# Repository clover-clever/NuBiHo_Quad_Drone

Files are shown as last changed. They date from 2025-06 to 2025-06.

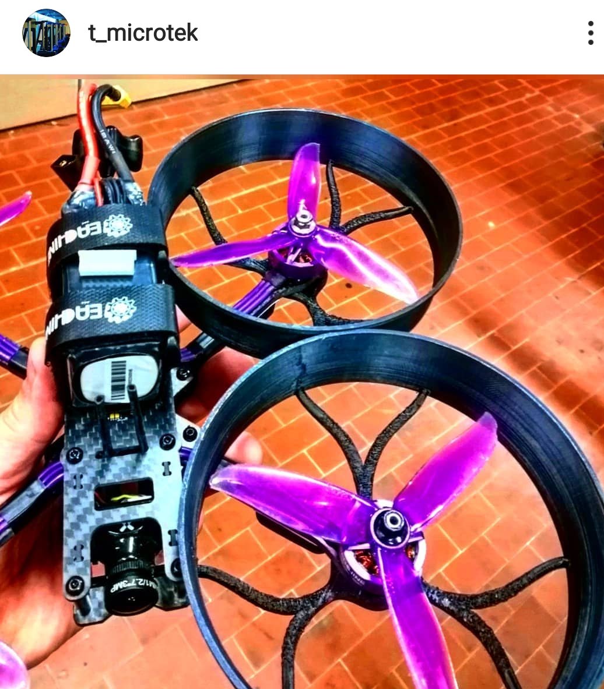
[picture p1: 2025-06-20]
NuBiHo_HW/Universal Propeller Guard Cover 5 inch - 4013765/images/Polish_20191201_160728039.jpg

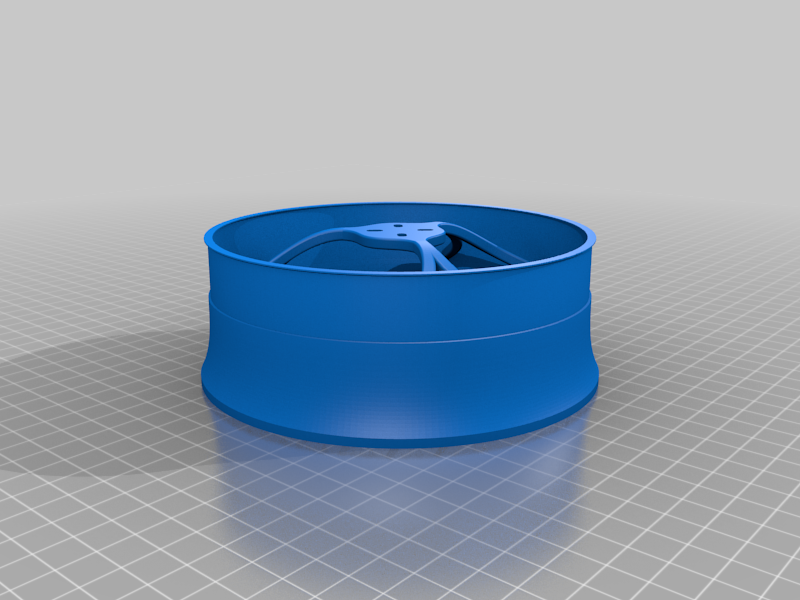
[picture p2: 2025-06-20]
NuBiHo_HW/Universal Propeller Guard Cover 5 inch - 4013765/images/propellers_cover_5inch_support.png

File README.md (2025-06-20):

2025, first semester Microprocessor Quad Drone Project

Based on Arduino Uno R3 for control with PPM Signal

PPM for SPRacing R3

Self-made PCBs
  - 6V Regulator does not work well,(Burnt)(delete 6V Switching Regulator and use it)
  - LM1117 - 12V --> 5V(too big voltage difference, do not use for high load, or just do not use it)

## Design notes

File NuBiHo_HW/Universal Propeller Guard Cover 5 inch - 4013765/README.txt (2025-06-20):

Universal Propeller Guard Cover 5 inch by TMicrotek on Thingiverse: https://www.thingiverse.com/thing:4013765

Summary:
Universal propeller guard will protect your propellers from impacts.One program already has the supports,while in the other you will have to insert them in the slicing program.If you like my things and want to support me, tips are welcome :)Have fun!

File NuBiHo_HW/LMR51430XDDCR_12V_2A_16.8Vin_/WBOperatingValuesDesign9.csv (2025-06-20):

Name | Value | Category | Description
Vout | 12 V | System Information | Operational Output Voltage
IC Tolerance | 10 mV | IC | IC Feedback Tolerance
Cin IRMS | 790.21 mA | Capacitor | Input capacitor RMS ripple current
Cin Pd | 4.16 mW | Capacitor | Input capacitor power dissipation
Cout IRMS | 30.67 mA | Capacitor | Output capacitor RMS ripple current
Cout Pd | 423.37 µW | Capacitor | Output capacitor power dissipation
Coutx IRMS | 56 mA | Capacitor | Output capacitor_x RMS ripple current
Coutx Pd | 13.23 µW | Capacitor | Output capacitor_x power loss
Cinx IRMS | 101.96 mA | Capacitor | Bulk capacitor RMS ripple current
Cinx Pd | 10.39 µW | Capacitor | Bulk capacitor power dissipation
L Ipp | 300.24 mA | Inductor | Peak-to-peak inductor ripple current
L Pd | 84.16 mW | Inductor | Inductor power dissipation
Ipp percentage | 15.01% | Inductor | Inductor ripple current percentage (with respect to average inductor current)
Duty Cycle | 72.89% | System Information | Duty cycle
Efficiency | 97% | System Information | Steady state efficiency
Frequency | 500 kHz | System Information | Switching frequency
IC Tj | 77.11 °C | IC | IC junction temperature
IC Pd | 654.32 mW | IC | IC power dissipation
Pout | 24 W | System Information | Total output power
Iin Avg | 1.47 A | IC | Average input current
IC Ipk | 2.15 A | IC | Peak switch current in IC
Mode | CCM | System Information | Conduction Mode
Vout p-p | 47.81 mV | System Information | Peak-to-peak output ripple voltage
Vin p-p | 961.15 mV | System Information | Peak-to-peak input voltage
Phase Marg | 48.62 ° | System Information | Bode Plot Phase Margin
Cross Freq | 15.55 kHz | System Information | Bode plot crossover frequency
Low Freq Gain | 46.85 dB | System Information | Gain at 1Hz
Gain Marg | -24.07 dB | System Information | Bode Plot Gain Margin
ICThetaJA Effective | 72 °C/W | IC | Effective IC Junction-to-Ambient Thermal Resistance
Total Pd | 743.28 mW | Power | Total Power Dissipation
FootPrint | 460 mm² | System Information | Total Foot Print Area of BOM components
Vin | 16.8 V | System Information | Vin operating point
Iout | 2 A | System Information | Iout operating point
Cin Pd | 4.16 mW | Power | Input capacitor power dissipation
Cout Pd | 423.37 µW | Power | Output capacitor power dissipation
Coutx Pd | 13.23 µW | Power | Output capacitor_x power loss
Cinx Pd | 10.39 µW | Power | Bulk capacitor power dissipation
L Pd | 84.16 mW | Power | Inductor power dissipation
IC Pd | 654.32 mW | Power | IC power dissipation
Vout Actual | 12.06 V | System Information | Vout Actual calculated based on selected voltage divider resistors
Vout Tolerance | 3.62% | System Information | Vout Tolerance based on IC Tolerance (no load) and voltage divider resistors if applicable
Total BOM | $3.36 | System Information | Total BOM Cost
BOM Count | 11 | System Information | Total Design BOM count

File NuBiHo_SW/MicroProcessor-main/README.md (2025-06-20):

# MicroProcessor

## Team
- 김민우
- 김재영
- 이상훈

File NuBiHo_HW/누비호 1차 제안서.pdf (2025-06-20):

# 마이크로프로세서응용시스템 제안서 발표

4조

### 2020099052 김재영 2020063063 김민우 2020028659 이상훈

# 누비호

## 1.문제 인식 배경

## 2.구현 목표

## 3.예상되는 어려움

## 4.구매 예정 물품

## 5.추후 계획

# CONTENTS

# 01 문제 인식 배경

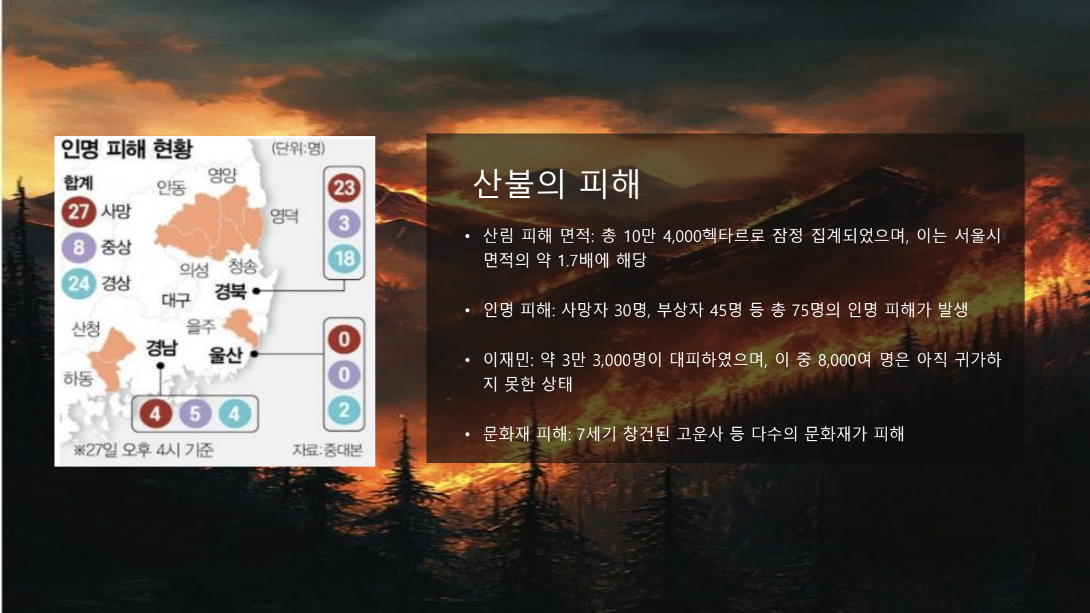
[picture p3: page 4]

Hong Hyun You 4

# 산불의 피해

- 산림 피해 면적: 총 10만 4,000헥타르로 잠정 집계되었으며, 이는 서울시 면적의 약 1.7배에 해당
- 인명 피해: 사망자 30명, 부상자 45명 등 총 75명의 인명 피해가 발생
- 이재민: 약 3만 3,000명이 대피하였으며, 이 중 8,000여 명은 아직 귀가하 지 못한 상태
- 문화재 피해: 7세기 창건된 고운사 등 다수의 문화재가 피해

## 문제 인식 배경

## 산악지형 접근성

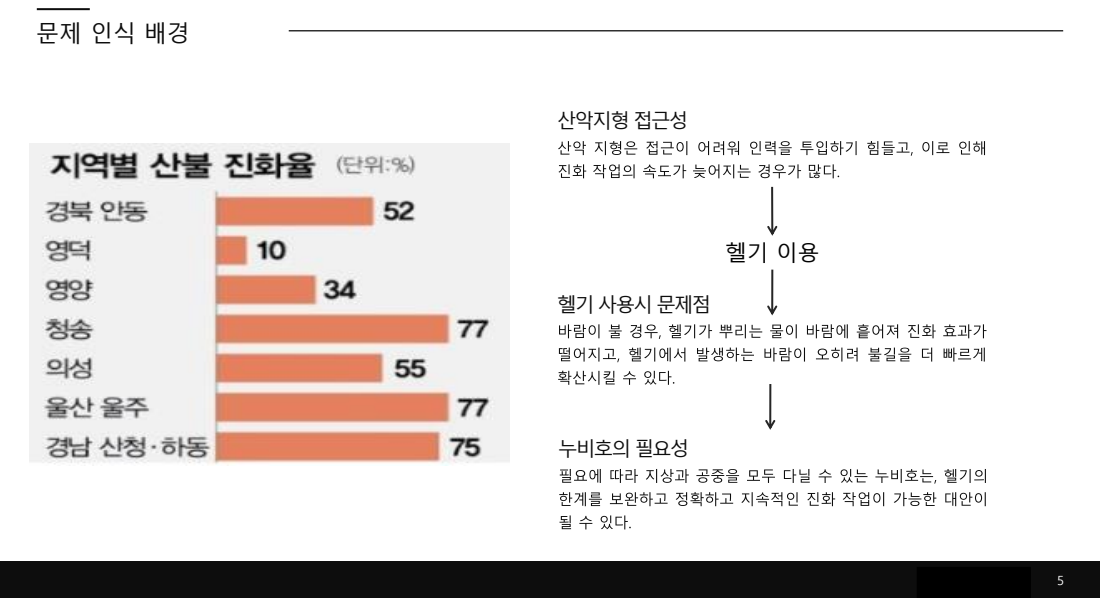
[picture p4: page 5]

산악 지형은 접근이 어려워 인력을 투입하기 힘들고, 이로 인해
진화 작업의 속도가 늦어지는 경우가 많다.

헬기 사용시 문제점
바람이 불 경우, 헬기가 뿌리는 물이 바람에 흩어져 진화 효과가
떨어지고, 헬기에서 발생하는 바람이 오히려 불길을 더 빠르게
확산시킬 수 있다.

누비호의 필요성
필요에 따라 지상과 공중을 모두 다닐 수 있는 누비호는, 헬기의
한계를 보완하고 정확하고 지속적인 진화 작업이 가능한 대안이

# 02 구현 목표

## 구현 목표

## 육공 양용 기능

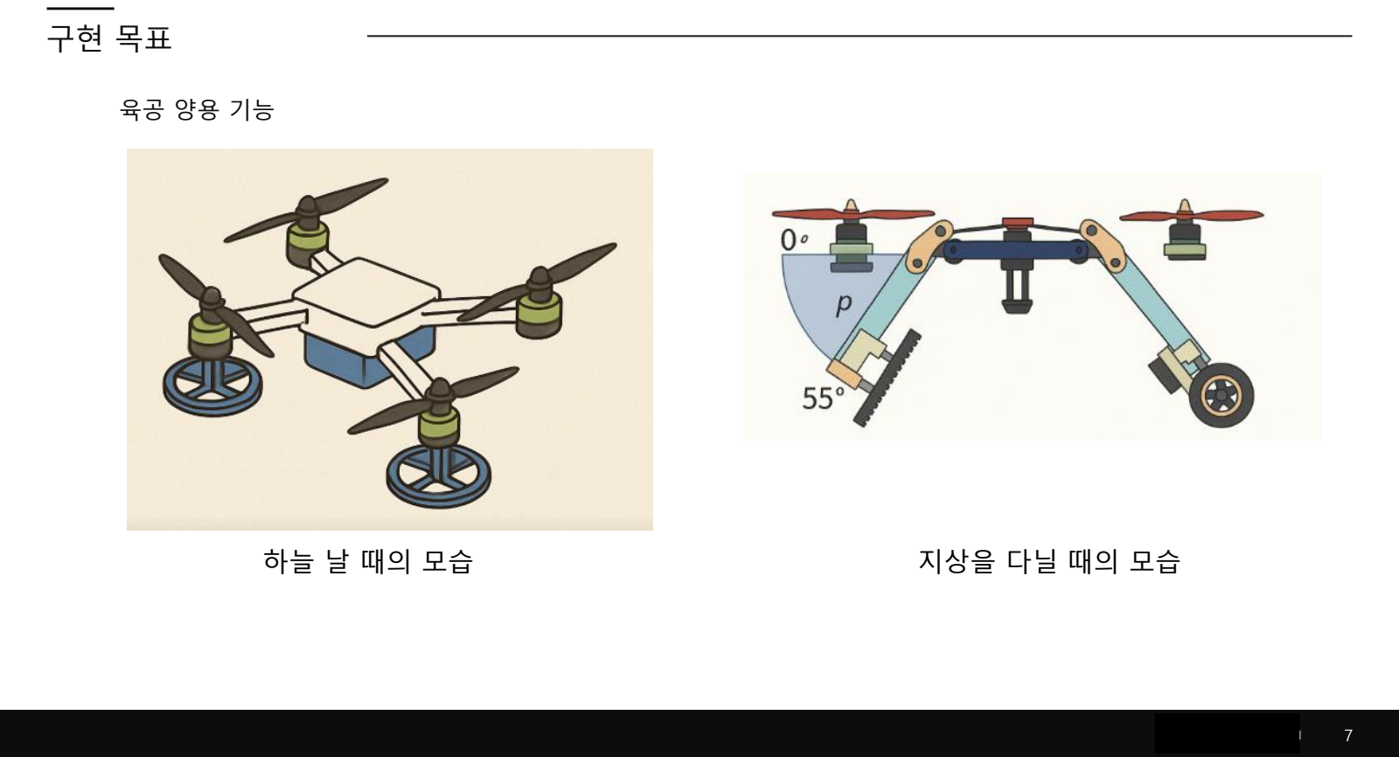
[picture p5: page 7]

하늘 날 때의 모습 | 지상을 다닐 때의 모습

## 구현 목표

## 소방 기능

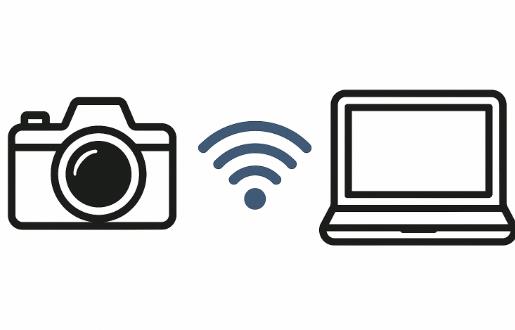
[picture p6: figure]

- 이미지 분석을 컴퓨터에서 수행
- 라즈베리파이에서 직접 이미지를 판단하려 했으나, 처리 속도 가 느려 실시간 분석에는 적합하지 않다고 판단

### WI-FI 사용 이유

# 03 예상되는 어려움

## 예상되는 어려움

- 프로펠러와 바퀴 간의 전환 시스템의 정밀한 기술이 필요

## 기계 설계의 복잡성

기계 설계

이미지 인식

드론 모터 제어

환경 조건

## 난이도

하 | 상
- 실제 원하는 이미지를 정확히 구분할 수 있는지 의문
- 데이터를 컴퓨터로 보내 컴퓨터가 판단할 수 있도록 계획

## 이미지 인식 기술

- 공중에 떠서 움직일 수 있도록 모터 4개를 안정적으로 제 어하기 어렵다 생각
- 드론 모터 제어에 효과적인 추가 프로세서를 구성

## 드론의 안정성 문제

- 다양한 환경의 영향을 받음
- 안정적인 실내에서 일단 구동 후 점차 보완

## 환경 조건에 따른 안정성

# 04 구매 예정 물품

## 구매 예정 물품 (1)

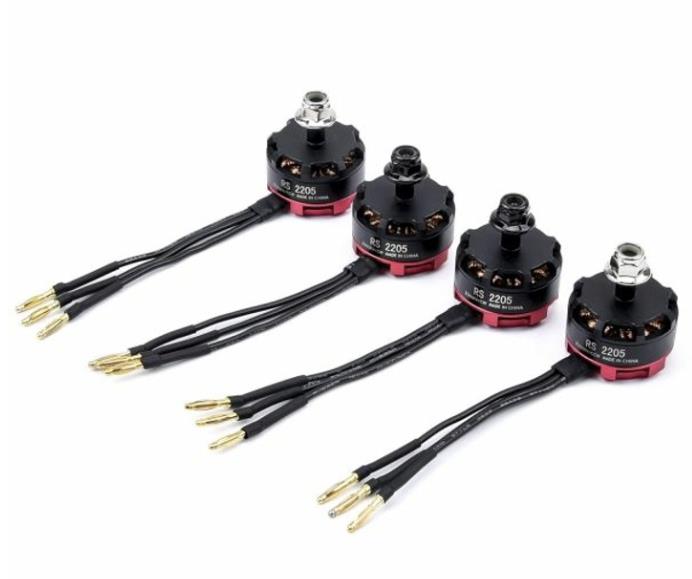
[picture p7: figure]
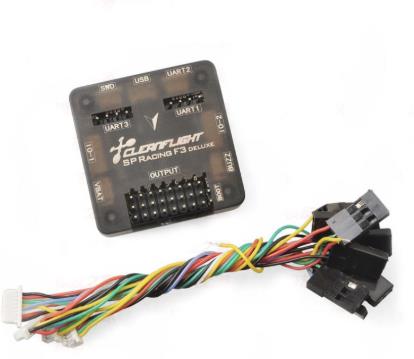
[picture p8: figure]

- 드론의 프로펠러와 바퀴 돌리는 역
할
- CW, CCW 각각 2개

### BLDC 모터

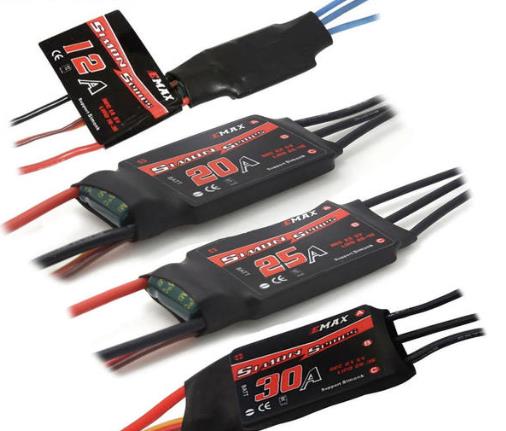
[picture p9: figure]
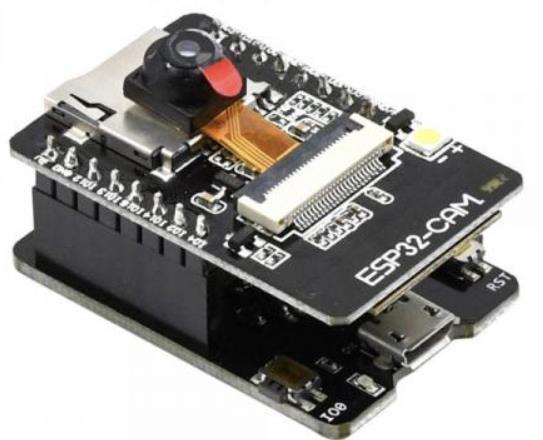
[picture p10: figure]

- BLDC 모터의 회전 속도 제어

## 멀티 변속기

- 비행의 두뇌 역할
- 기본적인 자세 제어

### Flight Controller

- 카메라와 WiFi 통신 기능을 모두 갖

춘 소형 보드
- 드론에 붙여 실시간 영상 전송

### ESP32- 캠

## 구매 예정 물품 (2)

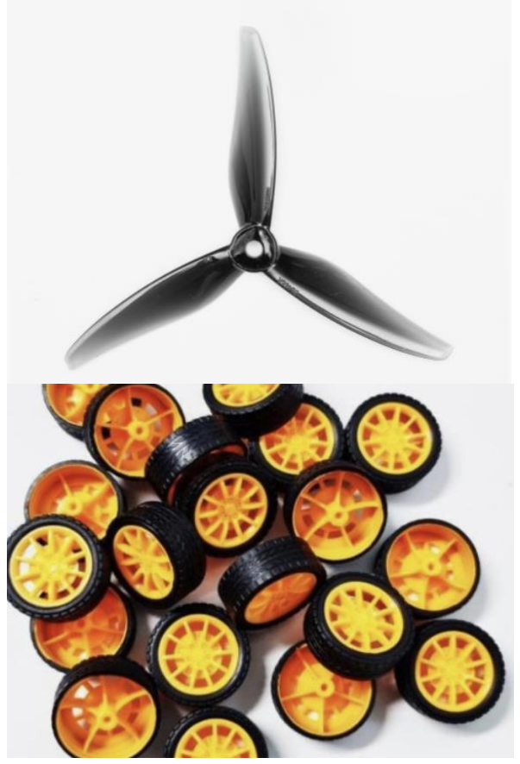
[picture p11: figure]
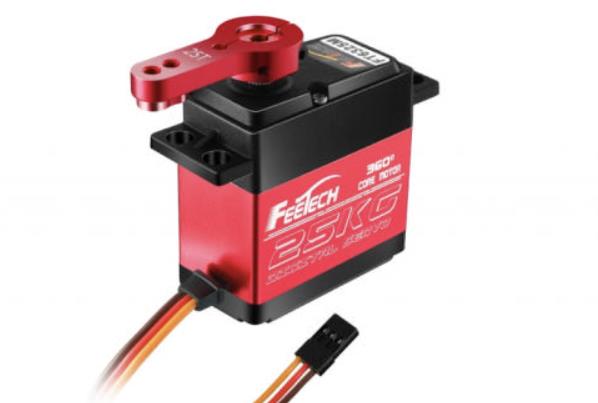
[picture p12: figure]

- 양쪽 날개를 동시에 접을 수 있도록
구동
- 두 개를 사용하는 것은 무겁기 때문
에, 하나만으로 접을 수 있는 구조로
설계

## 서보모터

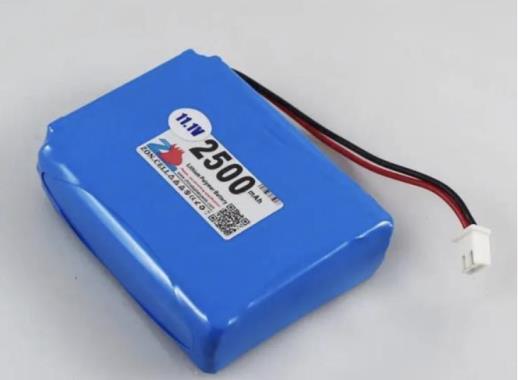
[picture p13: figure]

- 전력을 공급하는 배터리

## 리튬 이온 전지

- 모터에 직접 연결되어 회전하며 날
개의 역할 수행

### 프로펠러

- 기어박스를 통해 속도를 조절하여
하나의 모터로 지상과 공중 모두 주
행 가능

바퀴

# 05 추후 계획

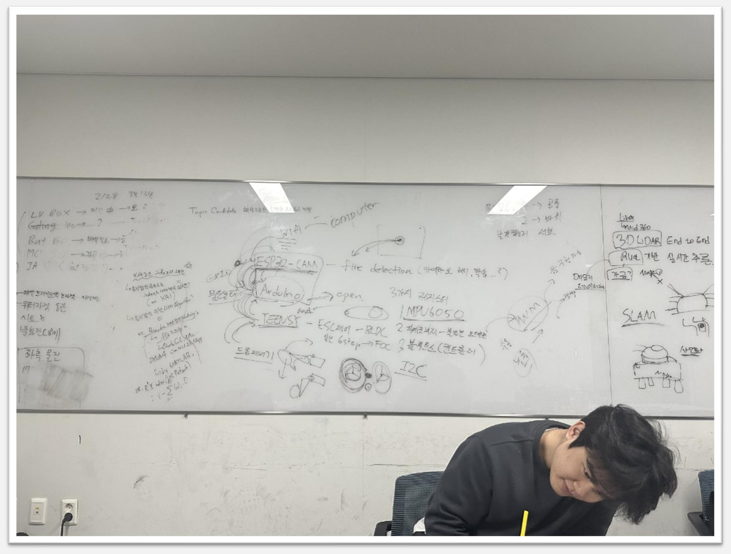
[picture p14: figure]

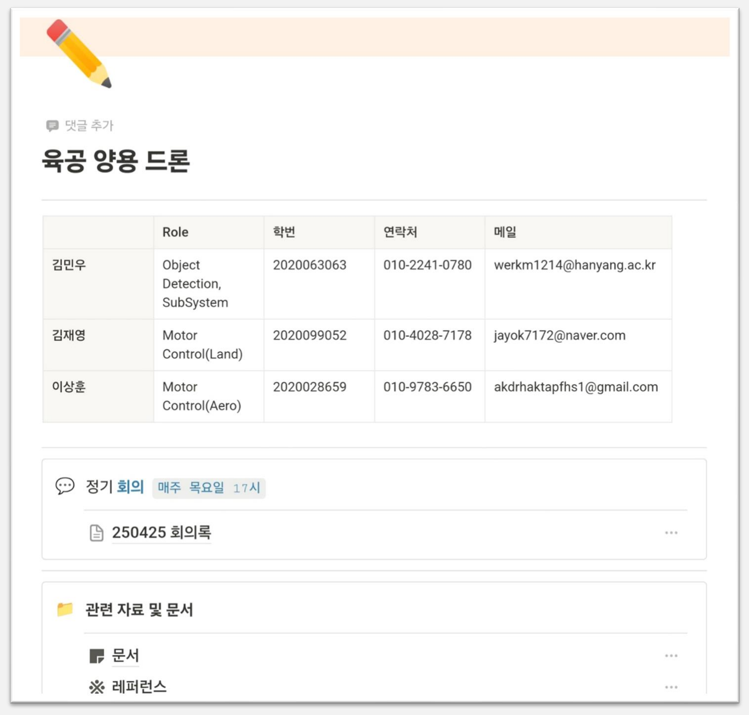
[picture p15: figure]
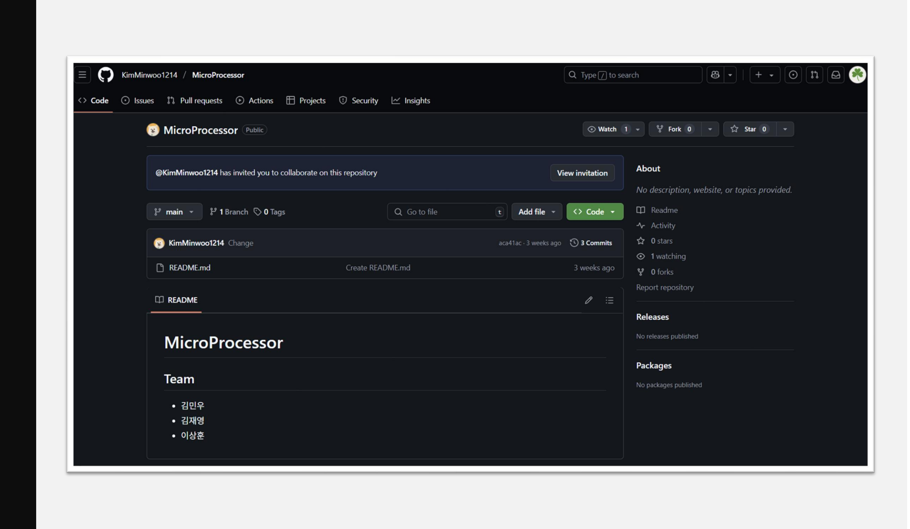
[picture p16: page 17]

## 추후 계획

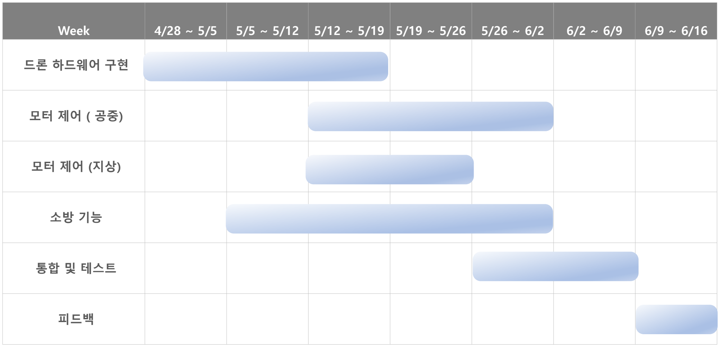
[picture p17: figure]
Week; 드론 하드웨어 구현; 통합 및 테스트; 피드백

# Thank you

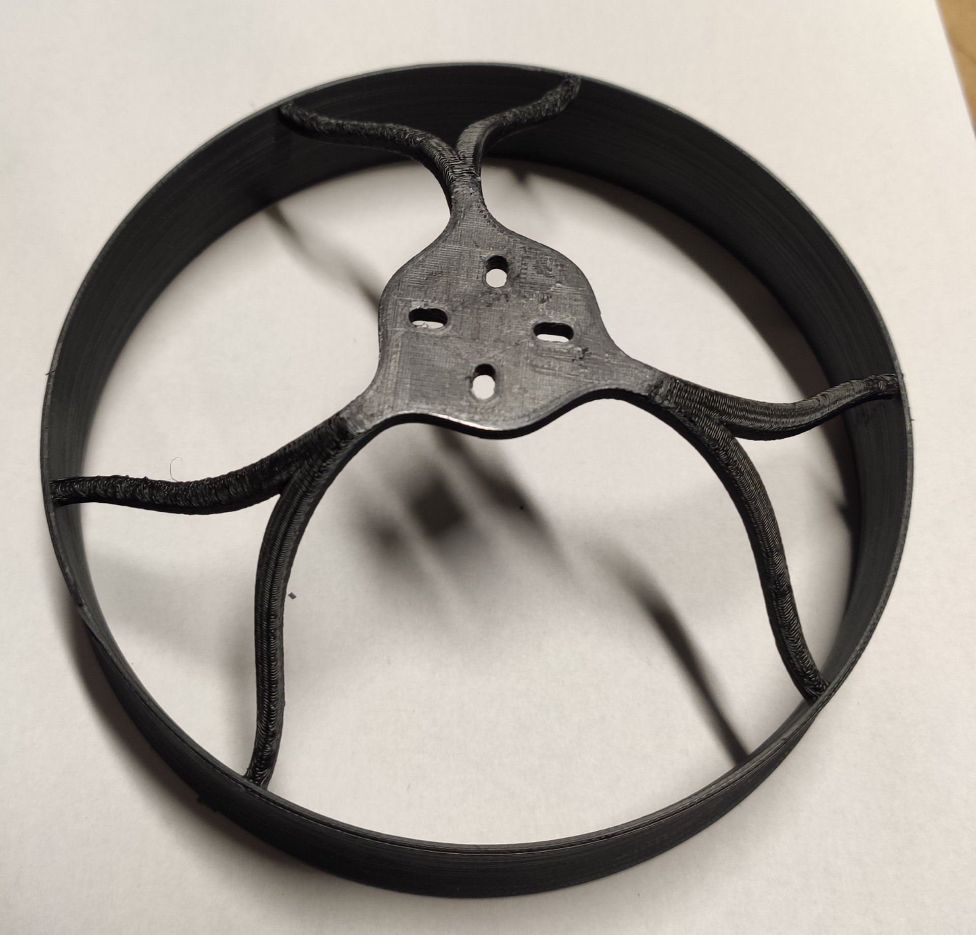
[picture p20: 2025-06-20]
NuBiHo_HW/Universal Propeller Guard Cover 5 inch - 4013765/images/Polish_20191201_160128843.jpg

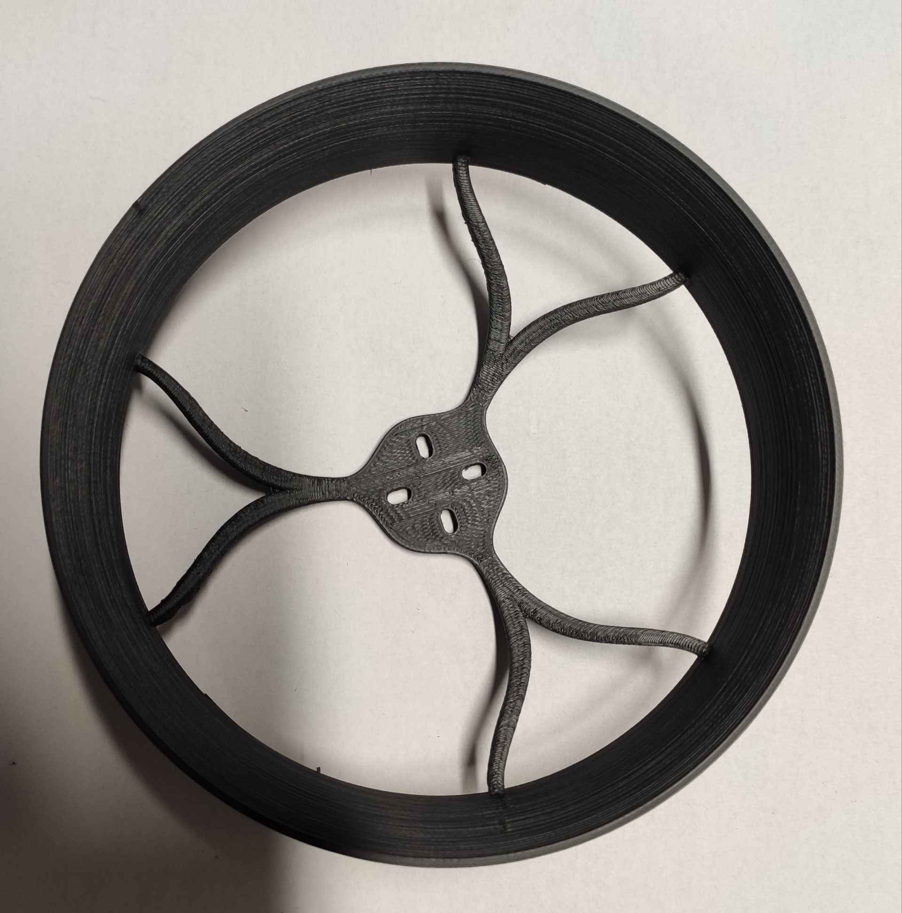
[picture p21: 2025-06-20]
NuBiHo_HW/Universal Propeller Guard Cover 5 inch - 4013765/images/Polish_20191201_160106141.jpg

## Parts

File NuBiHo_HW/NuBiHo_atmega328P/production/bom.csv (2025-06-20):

Designator | Footprint | Quantity | Value | LCSC Part #
A1 | Arduino_UNO_R3 | 1 | Arduino_UNO_R3
BZ1 | [GEC] G09B-5 | 1 | G09B-5
C1, C12, C23, C7, C9 | 0402 | 5 | 100nF
C10, C11, C8 | 0402 | 3 | 1uF
C13, C14, C2 | 0603 | 3 | 1uF
C15 | CP_EIA-6032-28_Kemet-C | 1 | 10uF
C16 | 1206 | 1 | 10uF
C17, C3 | 0805 | 2 | 100nF
C18, C19 | 1206 | 2 | 22uF
C20 | 1206 | 1 | 100nF
C21 | 0603 | 1 | 10nF
C22 | 0402 | 1 | 10uF
C24, C25 | CP_EIA-3528-21_Kemet-B | 2 | 10uF
C4 | 0805 | 1 | 2.2uF
C5, C6 | CP_EIA-3528-21_Kemet-B_Pad1.50x2.35mm_HandSolder | 2 | 10uF
D1 | D_SOD-123 | 1 | 1N4148W
D2 | D_SMA | 1 | SS14
D3, D4, D5 | 0805 | 3 | LED
D6 | 0805 | 1 | 5VD_LED
D7 | 0805 | 1 | 5VP_LED
J1 | PinHeader_1x10_P2.54mm_Vertical | 1 | MPU9250
J2 | AMASS_XT60-M_1x02_P7.20mm_Vertical | 1 | BATT/XT60
J3 | Molex_SPOX_5267-03A_1x03_P2.50mm_Vertical | 1 | MG-996R
J4 | Molex_SPOX_5267-04A_1x04_P2.50mm_Vertical | 1 | ESP32
J5 | Molex_SPOX_5267-02A_1x02_P2.50mm_Vertical | 1 | WaterValve
J6 | PinHeader_1x03_P2.54mm_Vertical | 1 | Conn_01x03_Pin
J7 | Molex_SPOX_5267-07A_1x07_P2.50mm_Vertical | 1 | FC
J8 | PinHeader_1x02_P2.54mm_Vertical | 1 | EN
J9 | PinHeader_1x06_P2.54mm_Vertical | 1 | HC-05
L1 | INDPM172172X700N | 1 | 22uH
L2 | L_Coilcraft_XAL4030-XXX | 1 | XAL4030-332MEB
Q1 | SOT-23 | 1 | BC847
Q2 | SOT-23 | 1 | AO3400A
Q3 | SOT-23 | 1 | 2N7002
R1, R2 | 0402 | 2 | 4.7k
R10 | 0603 | 1 | 10k
R11, R15 | 0402 | 2 | 1k
R12 | 0402 | 1 | 4.3k
R13, R14, R3 | 0402 | 3 | 47k
R16, R8 | 0402 | 2 | 100k
R17 | 0402 | 1 | 820
R18, R19, R20 | 0402 | 3 | 560
R4 | 0603 | 1 | 422kOhm
R5 | 0603 | 1 | 22.1kOhm
R6 | 0402 | 1 | 2.2kOhm
R7 | 0402 | 1 | 100
R9 | 0603 | 1 | 68.1k
U1, U2 | SSOP-8_2.95x2.8mm_P0.65mm | 2 | TXS0102DCT
U3 | SOT-23-6 | 1 | LMR51430XDDCR
U4, U5 | SOT-23-5 | 2 | 74LVC1G17
U6, U9 | SOT-223-3_TabPin2 | 2 | LM1117MP-5.0
U7 | SOT-23-6 | 1 | TPS563200DDCR
U8 | SOIC-8_3.9x4.9mm_P1.27mm | 1 | SE555D

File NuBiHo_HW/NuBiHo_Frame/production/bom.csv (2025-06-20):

Designator | Footprint | Quantity | Value | LCSC Part #
J1 | AMASS_XT60-M_1x02_P7.20mm_Vertical | 1 | Main
J2 | AMASS_XT60-M_1x02_P7.20mm_Vertical | 1 | FL
J3 | AMASS_XT60-M_1x02_P7.20mm_Vertical | 1 | FR
J4 | AMASS_XT60-M_1x02_P7.20mm_Vertical | 1 | RL
J5 | AMASS_XT60-M_1x02_P7.20mm_Vertical | 1 | RR

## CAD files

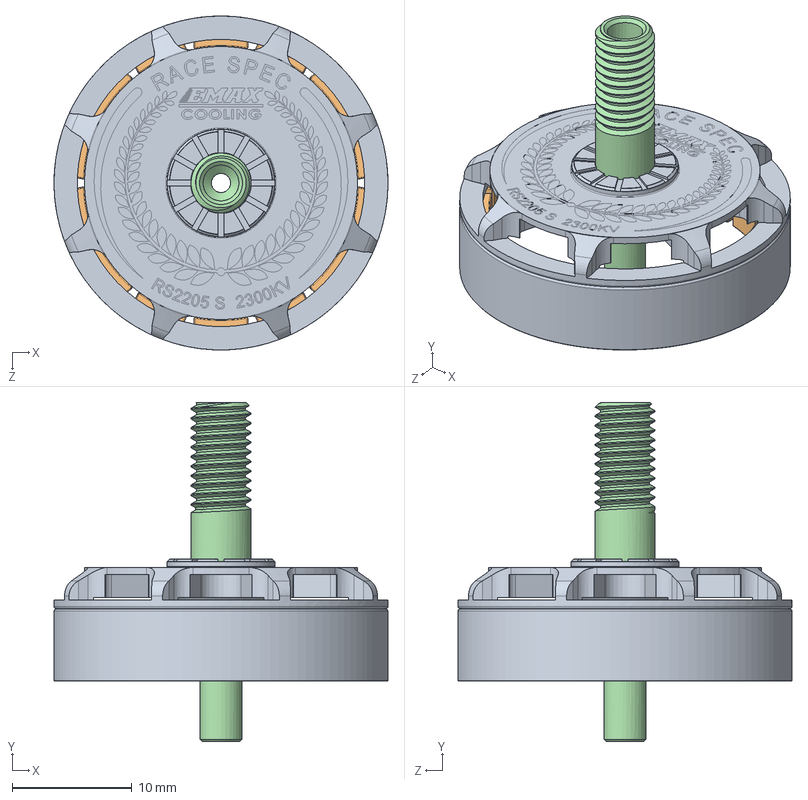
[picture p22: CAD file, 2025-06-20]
NuBiHo_HW/NubiHo/STP_files_out_source/EMAX RS2205 S/ROTOR.SLDASM
27.9 x 28.3 x 27.9 mm
ROTOR BELL
MAGNETS
MAGNETS ADHESIVE
SHAFT

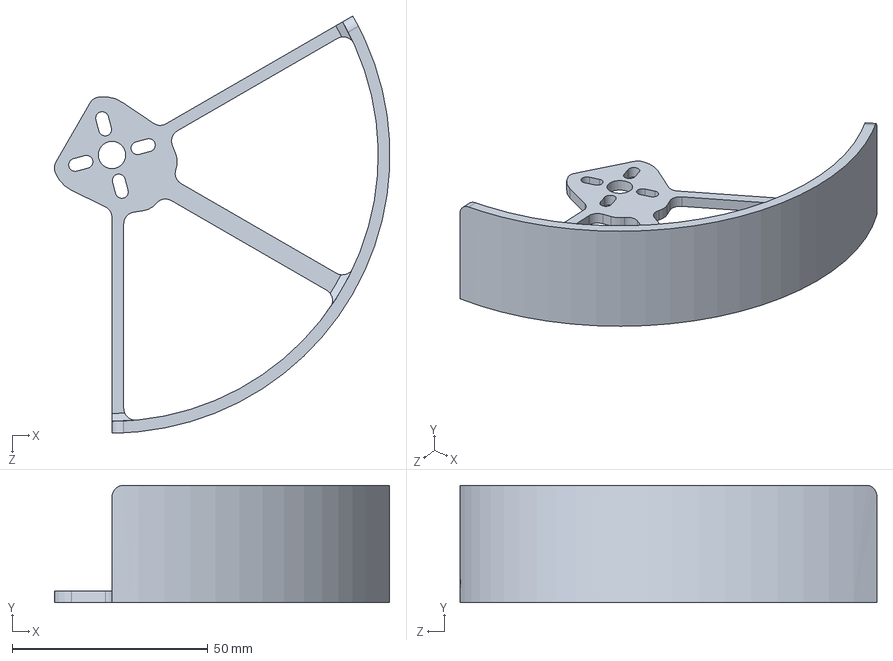
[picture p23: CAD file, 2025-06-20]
NuBiHo_HW/5-inch-propeller-guard-1.snapshot.2/propguard.SLDPRT
85.6 x 30.0 x 106.5 mm

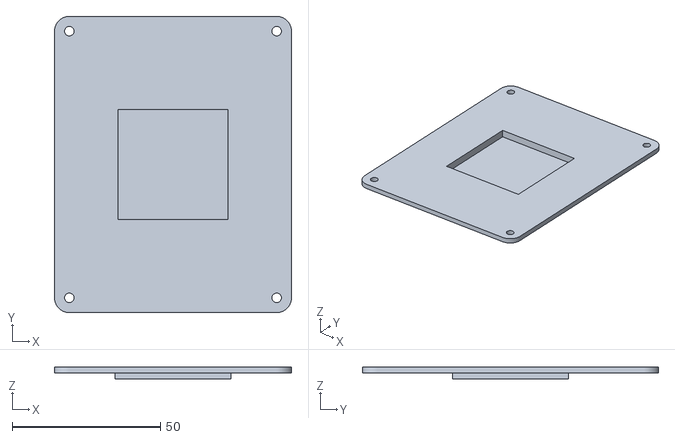
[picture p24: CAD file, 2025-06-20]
NuBiHo_HW/NubiHo/NuBiHo_SPRacing_Support.stl
80.0 x 100.0 x 4.00

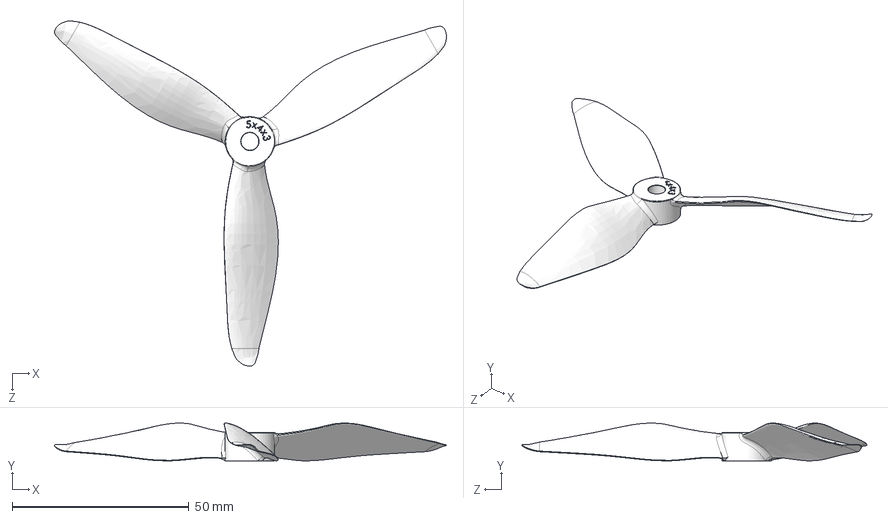
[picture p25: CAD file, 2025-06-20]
NuBiHo_HW/NubiHo/STP_files_out_source/5x4x3-propeller-1.snapshot.2/5x4x3.STEP
110.8 x 10.7 x 97.5 mm

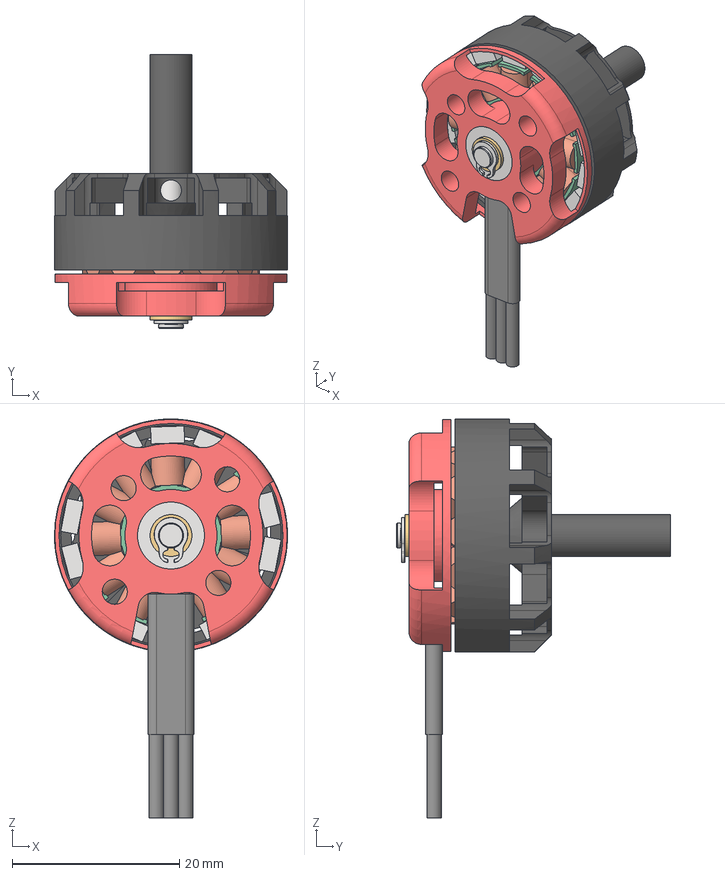
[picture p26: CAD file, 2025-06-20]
NuBiHo_HW/NubiHo/STP_files_out_source/akk-rs2205-2300kv-1.snapshot.1/AKK RS2205 2300KV.stp
27.8 x 32.8 x 47.7 mm
BASE
BEARING x 2
STATOR
CAN
SHAFT
98541A111_External Retaining Ring
SPACER
COILS x 12
Magnets x 14
Cable Sleeve

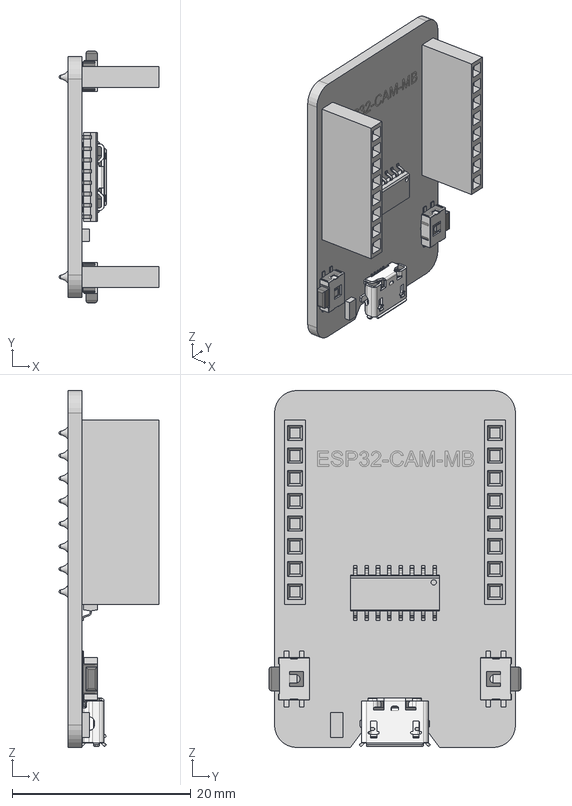
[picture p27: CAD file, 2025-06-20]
NuBiHo_HW/NubiHo/STP_files_out_source/esp32-cam-mb-esp32-cam-extension-board-1.snapshot.2/ESP32-CAM-MB.step
11.2 x 28.2 x 40.0 mm
User_Library-so16-1
YD-3414 - Side SMD Switch
YD-3414 - Side SMD Switch v1(Odbicie)
DIY MicroUSB Port

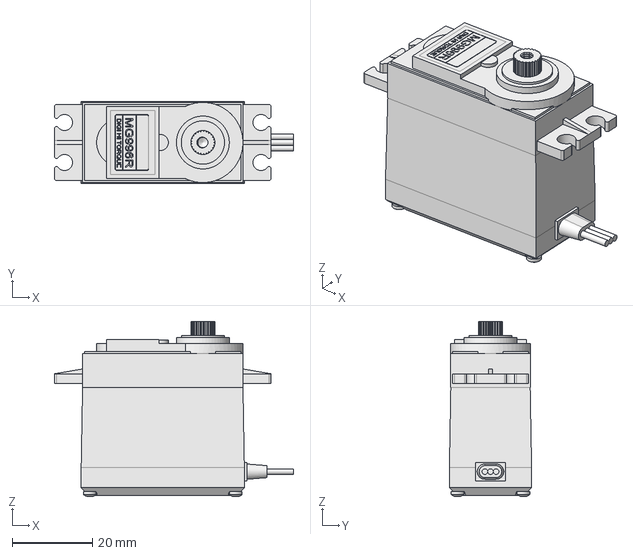
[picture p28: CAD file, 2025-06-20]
NuBiHo_HW/NubiHo/STP_files_out_source/mg996r-servo-3.snapshot.9/mg996R_v2.FCStd
59.6 x 20.5 x 43.8 mm

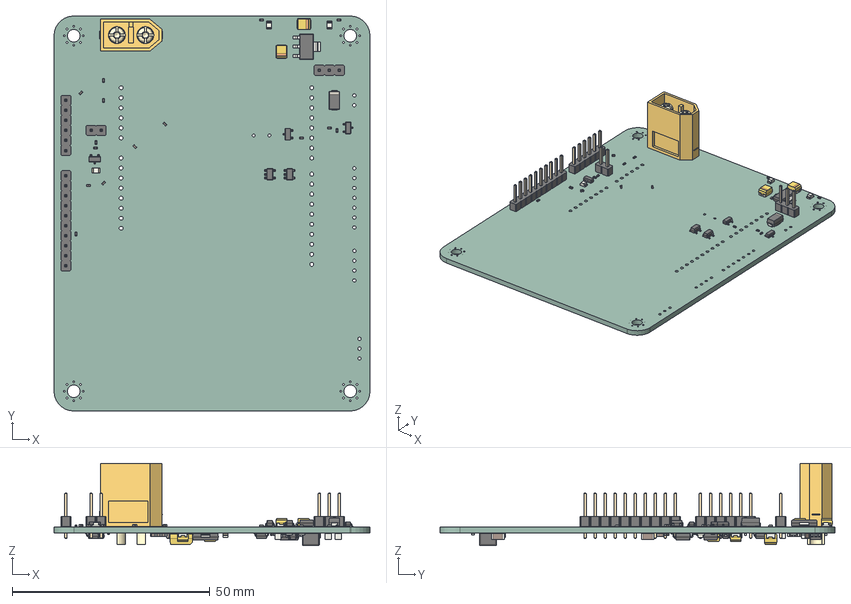
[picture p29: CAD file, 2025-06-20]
NuBiHo_HW/NubiHo/STP_files_out_source/NuBiHo_atmega328P.step
80.0 x 100.0 x 20.8 mm
R_0402_1005Metric x 16
PinHeader_1x02_P254mm_Vertical
LED_0805_2012Metric x 5
SOT_23_5 x 2
C_0402_1005Metric x 9
SOT_23 x 3
CP_EIA_3528_21_Kemet_B x 4
PinHeader_1x10_P254mm_Vertical
SOT_223 x 2
PinHeader_1x03_P254mm_Vertical
PinHeader_1x06_P254mm_Vertical
XT60 male v9
D_SMA
CQ assembly
R_0603_1608Metric x 4
C_1206_3216Metric x 4
D_SOD_123
C_0805_2012Metric x 3
C_0603_1608Metric x 4
SSOP_8_295x28mm_P065mm x 2
SOIC_8_39x49mm_P127mm
CP_EIA_6032_28_Kemet_C
SOT_23_6 x 2
NuBiHo_atmega328P_PCB

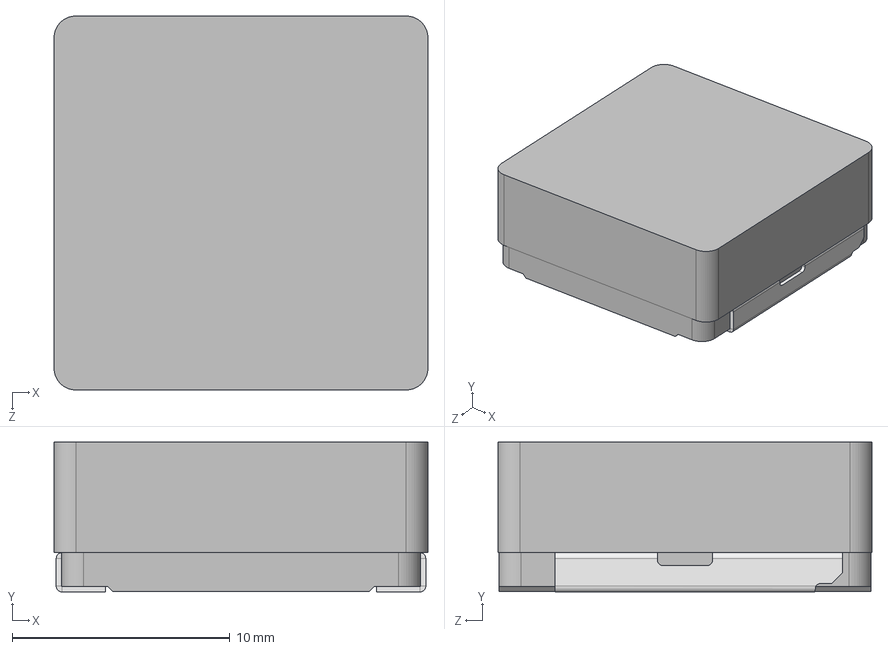
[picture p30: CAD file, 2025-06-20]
NuBiHo_HW/NuBiHo_atmega328P/LIB_IHLP6767GZER220M11/IHLP6767GZER220M11/3D/IHLP6767GZER220M11.stp
17.2 x 6.88 x 17.2 mm

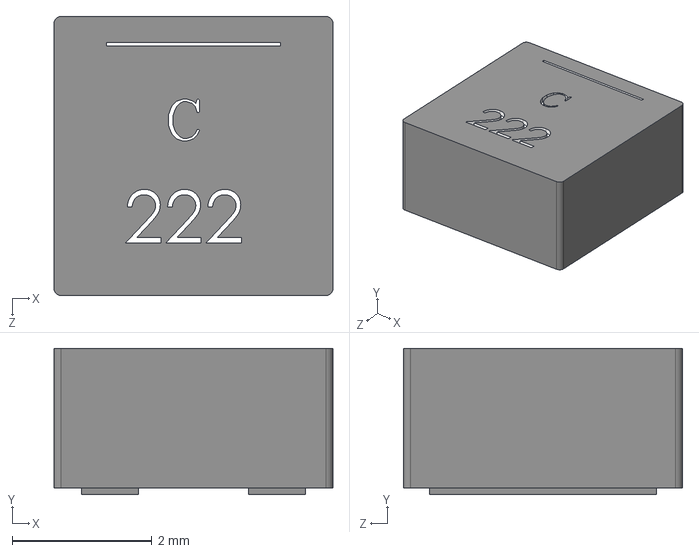
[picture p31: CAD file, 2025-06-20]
NuBiHo_HW/NuBiHo_atmega328P/LIB_XAL4030-332MEC/XAL4030-332MEC/3D/XAL4030-332MEC.stp
4.00 x 2.10 x 4.00 mm

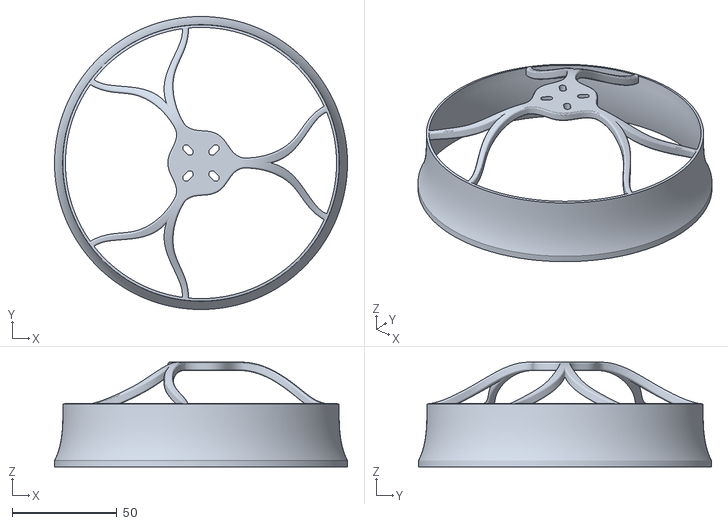
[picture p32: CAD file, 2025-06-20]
NuBiHo_HW/Universal Propeller Guard Cover 5 inch - 4013765/files/propellers_cover_5inch.STL
140.0 x 140.0 x 50.0

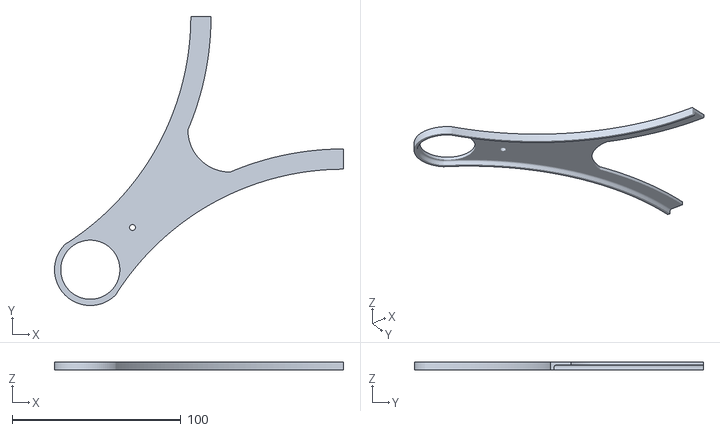
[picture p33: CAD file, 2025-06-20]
NuBiHo_HW/NubiHo/NuBiHo_Frame_PCB_Support.stl
171.2 x 171.2 x 5.00

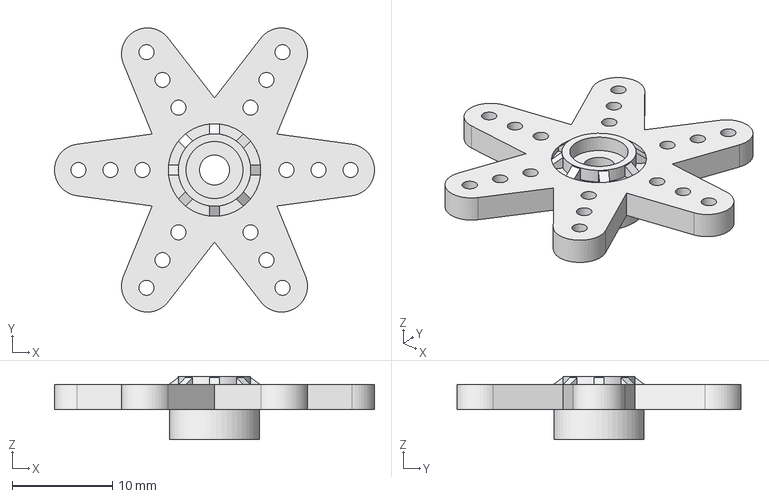
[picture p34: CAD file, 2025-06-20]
NuBiHo_HW/NubiHo/STP_files_out_source/mg996r-servo-3.snapshot.9/mg996_arm_6pad.step
32.0 x 28.4 x 6.30 mm

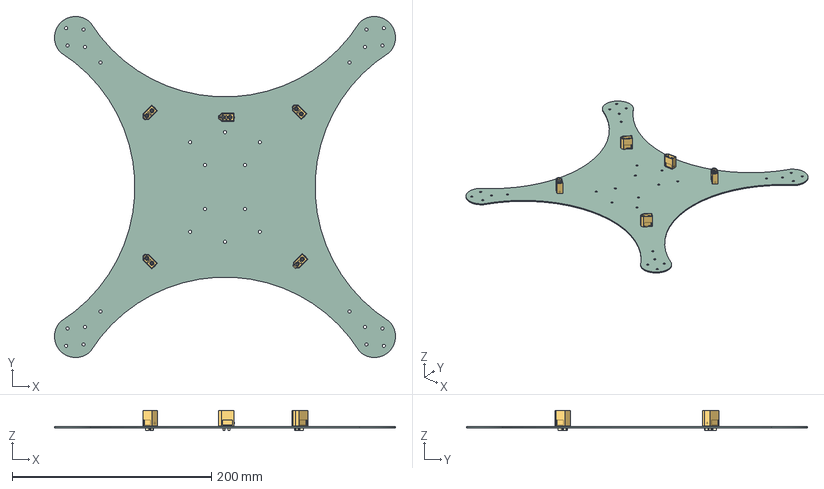
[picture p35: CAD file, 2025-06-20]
NuBiHo_HW/NuBiHo_Frame/NuBiHo_Frame_V3.step
342.3 x 342.3 x 20.5 mm
AMASS_XT60-M_1x02_P7.2mm_Vertical x 5
NuBiHo_Frame_PCB

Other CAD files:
NuBiHo_HW/Universal Propeller Guard Cover 5 inch - 4013765/files/propellers_cover_5inch_support.STL
NuBiHo_HW/NubiHo/NuBiHo_Body_Frame.step
NuBiHo_HW/NubiHo/STP_files_out_source/EMAX RS2205 S/STATOR.SLDPRT
NuBiHo_HW/NubiHo/STP_files_out_source/mg996r-servo-3.snapshot.9/mg996_arms.FCStd
NuBiHo_HW/5-inch-propeller-guard-1.snapshot.2/propguard.STL
NuBiHo_HW/NuBiHo_Frame/NuBiHo_Frame_V2.step
NuBiHo_HW/NuBiHo_atmega328P/LIB_IHLP6767GZER220M11/IHLP6767GZER220M11/Allegro/indpm172172x700n.psm
NuBiHo_HW/NuBiHo_atmega328P/LIB_IHLP6767GZER220M11/IHLP6767GZER220M11/DEHDL/ihlp6767gzer220m11/chips/chips.prt
NuBiHo_HW/NuBiHo_atmega328P/LIB_XAL4030-332MEC/XAL4030-332MEC/Allegro/xal40xx.psm
NuBiHo_HW/NuBiHo_atmega328P/LIB_XAL4030-332MEC/XAL4030-332MEC/DEHDL/xal4030_332mec/chips/chips.prt
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

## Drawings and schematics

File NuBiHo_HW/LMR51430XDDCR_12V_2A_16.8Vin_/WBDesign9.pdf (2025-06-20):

## WEBENCH ® Design Report

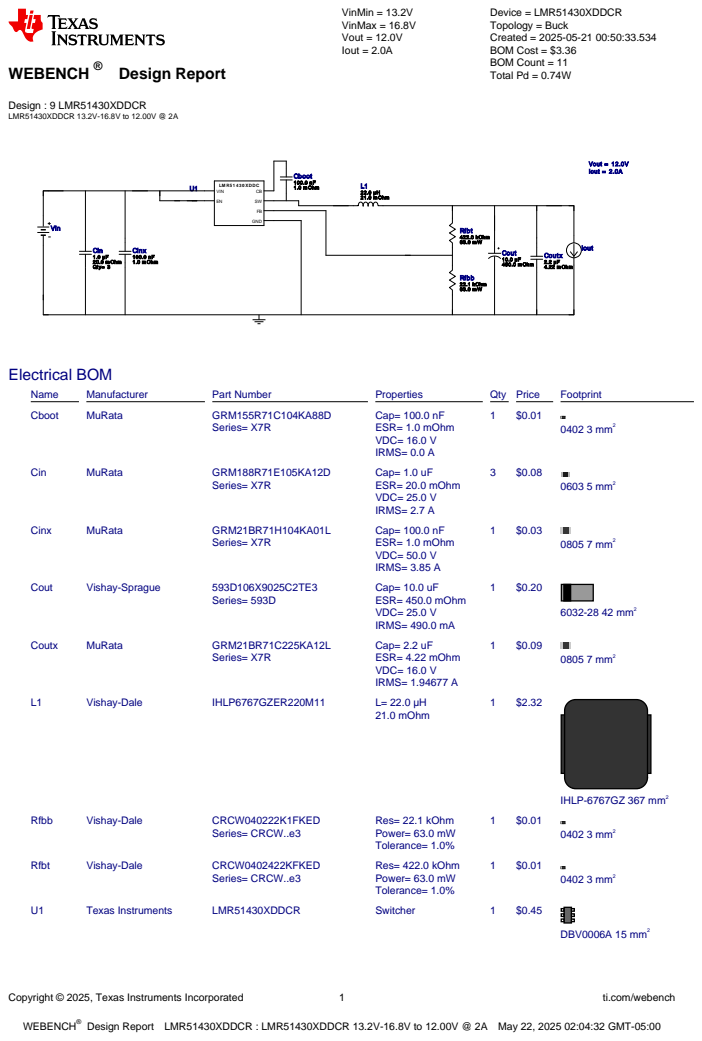
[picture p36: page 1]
Copyright © 2025, Texas Instruments Incorporated; ti.com/webench; WEBENCH®; Design : 9 LMR51430XDDCR LMR51430XDDCR 13.2V-16.8V to 12.00V @ 2A; VinMin = 13.2V VinMax = 16.8V Vout = 12.0V Iout = 2.0A; Device = LMR51430XDDCR Topology = Buck Created = 2025-05-21 00:50:33.534 BOM Cost = $3.36 BOM Count = 11 Total Pd = 0.74W; Cin 1.0 µF 20.0 m Ohm Qty= 3; LM R5 1 4 3 0 XDDC; GND; VIN; Cout 10.0 µF 450.0 m Ohm; Cinx 100.0 nF 1.0 m Ohm; L1 22.0 µH 21.0 m Ohm; Coutx 2.2 µF 4.22 m Ohm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

Design Report LMR51430XDDCR : LMR51430XDDCR 13.2V-16.8V to 12.00V @ 2A May 22, 2025 02:04:32 GMT-05:00

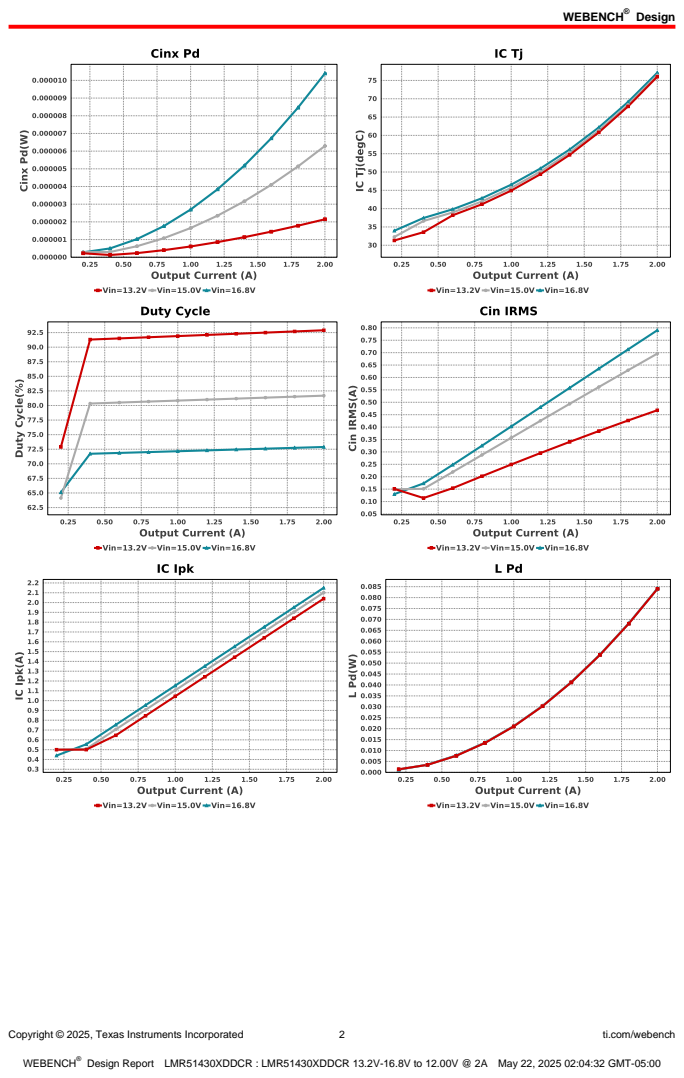
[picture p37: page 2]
Design; Copyright © 2025, Texas Instruments Incorporated; ti.com/webench

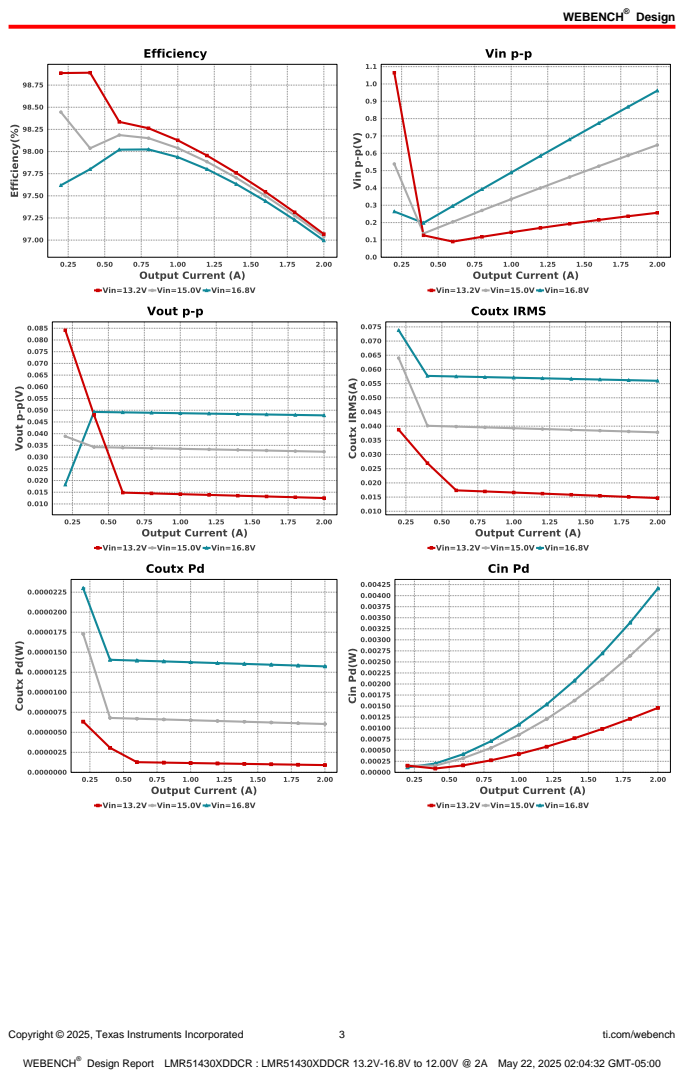
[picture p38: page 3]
Copyright © 2025, Texas Instruments Incorporated; ti.com/webench

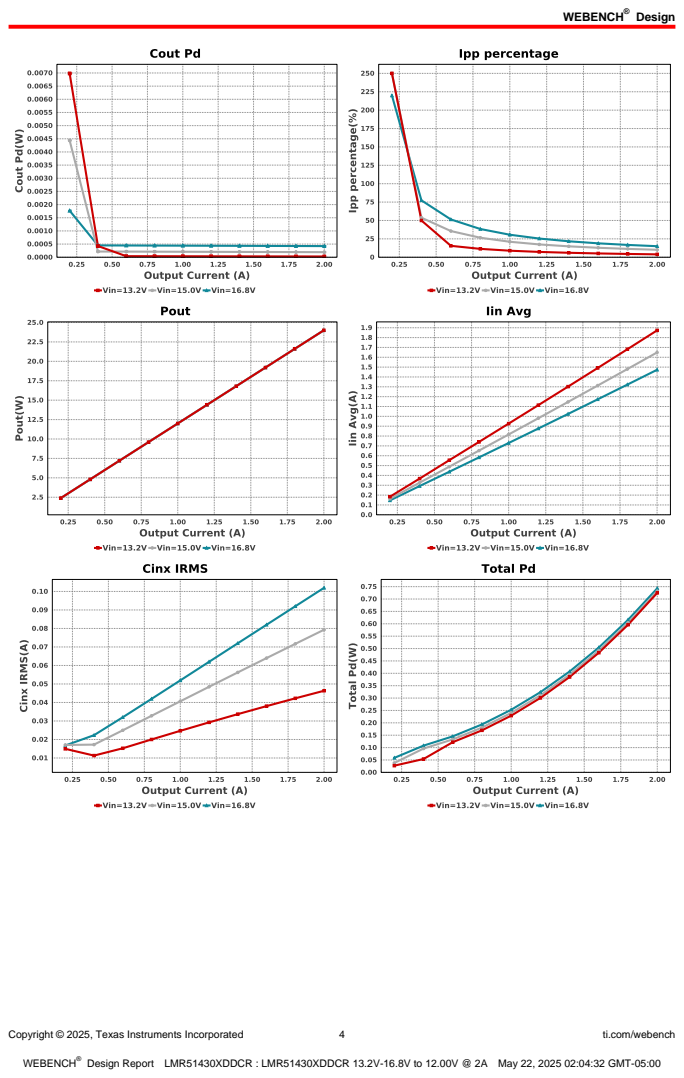
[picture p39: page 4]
Copyright © 2025, Texas Instruments Incorporated; ti.com/webench

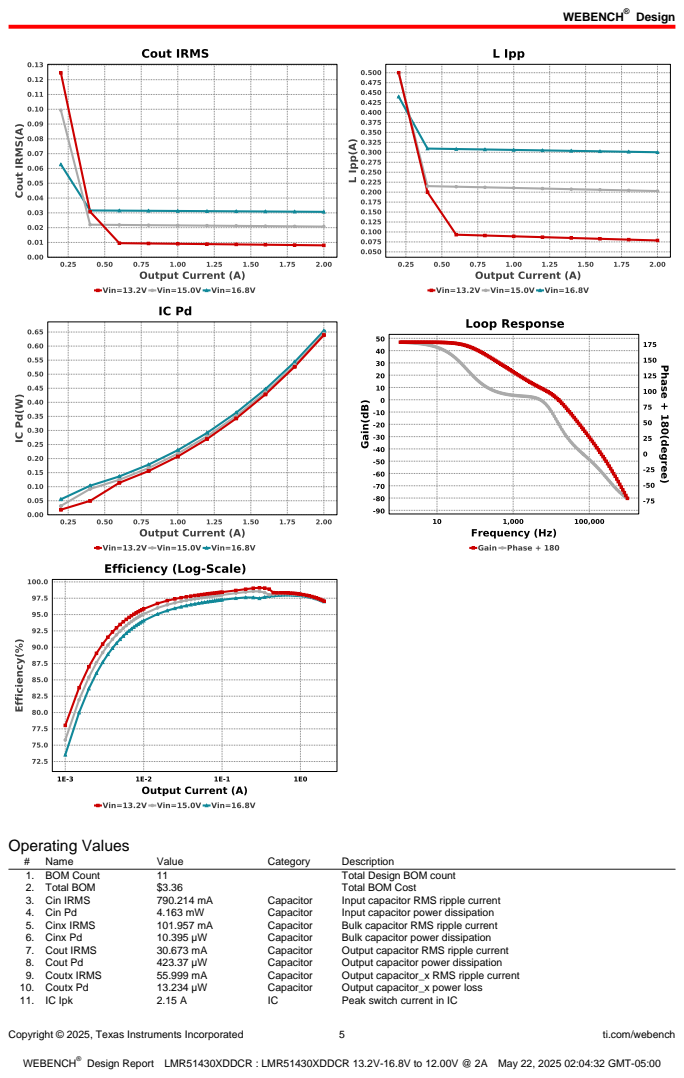
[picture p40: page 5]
Copyright © 2025, Texas Instruments Incorporated; ti.com/webench; Operating Values; Name; Value; Category; Description; 1. BOM Count; Total Design BOM count; 2. Total BOM; Total BOM Cost; 3. Cin IRMS; Capacitor; Input capacitor RMS ripple current; 4. Cin Pd; Input capacitor power dissipation; 5. Cinx IRMS; Bulk capacitor RMS ripple current; 6. Cinx Pd; Bulk capacitor power dissipation; 7. Cout IRMS; Output capacitor RMS ripple current; 8. Cout Pd; Output capacitor power dissipation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

Copyright © 2025, Texas Instruments Incorporated | 6 | ti.com/webench
# | Name | Value | Category | Description

12. IC Pd | 654.32 mW | IC | IC power dissipation
13. IC Tj | 77.111 degC | IC | IC junction temperature
14. IC Tolerance | 10.0 mV | IC | IC Feedback Tolerance
15. ICThetaJA Effective | 72.0 degC/W | IC | Effective IC Junction-to-Ambient Thermal Resistance
16. Iin Avg | 1.473 A | IC | Average input current
17. Ipp percentage | 15.012 % | Inductor | Inductor ripple current percentage (with respect to average inductor
| | | | current)
18. L Ipp | 300.241 mA | Inductor | Peak-to-peak inductor ripple current
19. L Pd | 84.158 mW | Inductor | Inductor power dissipation
20. Cin Pd | 4.163 mW | Power | Input capacitor power dissipation
21. Cinx Pd | 10.395 µW | Power | Bulk capacitor power dissipation
22. Cout Pd | 423.37 µW | Power | Output capacitor power dissipation
23. Coutx Pd | 13.234 µW | Power | Output capacitor_x power loss
24. IC Pd | 654.32 mW | Power | IC power dissipation
25. L Pd | 84.158 mW | Power | Inductor power dissipation
26. Total Pd | 743.281 mW | Power | Total Power Dissipation
27. Cross Freq | 15.553 kHz | System
| | | Information | Bode plot crossover frequency
28. Duty Cycle | 72.886 % | System
| | | Information | Duty cycle
29. Efficiency | 96.996 % | System
| | | Information | Steady state efficiency
30. FootPrint | 460.0 mm² | System
| | | Information | Total Foot Print Area of BOM components
31. Frequency | 500.0 kHz | System
| | | Information | Switching frequency
32. Gain Marg | -24.066 dB | System
| | | Information | Bode Plot Gain Margin
33. Iout | 2.0 A | System
| | | Information | Iout operating point
34. Low Freq Gain | 46.855 dB | System
| | | Information | Gain at 1Hz
35. Mode | CCM | System
| | | Information | Conduction Mode
36. Phase Marg | 48.623 deg | System
| | | Information | Bode Plot Phase Margin
37. Pout | 24.0 W | System
| | | Information | Total output power
38. Vin | 16.8 V | System
| | | Information | Vin operating point
39. Vin p-p | 961.15 mV | System
| | | Information | Peak-to-peak input voltage
40. Vout | 12.0 V | System
| | | Information | Operational Output Voltage
41. Vout Actual | 12.057 V | System
| | | Information | Vout Actual calculated based on selected voltage divider resistors
42. Vout Tolerance | 3.618 % | System
| | | Information | Vout Tolerance based on IC Tolerance (no load) and voltage divider resistors if applicable
43. Vout p-p | 47.814 mV | System
| | | Information | Peak-to-peak output ripple voltage

## Design Inputs

Name | Value | Description
Iout | 2.0 | Maximum Output Current
VinMax | 16.8 | Maximum input voltage
VinMin | 13.2 | Minimum input voltage
Vout | 12.0 | Output Voltage
| base_pn | | LMR51430X | Base Product Number
source | DC | Input Source Type
Ta | 30.0 | Ambient temperature


Copyright © 2025, Texas Instruments Incorporated | 7 | ti.com/webench

## Assembly
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

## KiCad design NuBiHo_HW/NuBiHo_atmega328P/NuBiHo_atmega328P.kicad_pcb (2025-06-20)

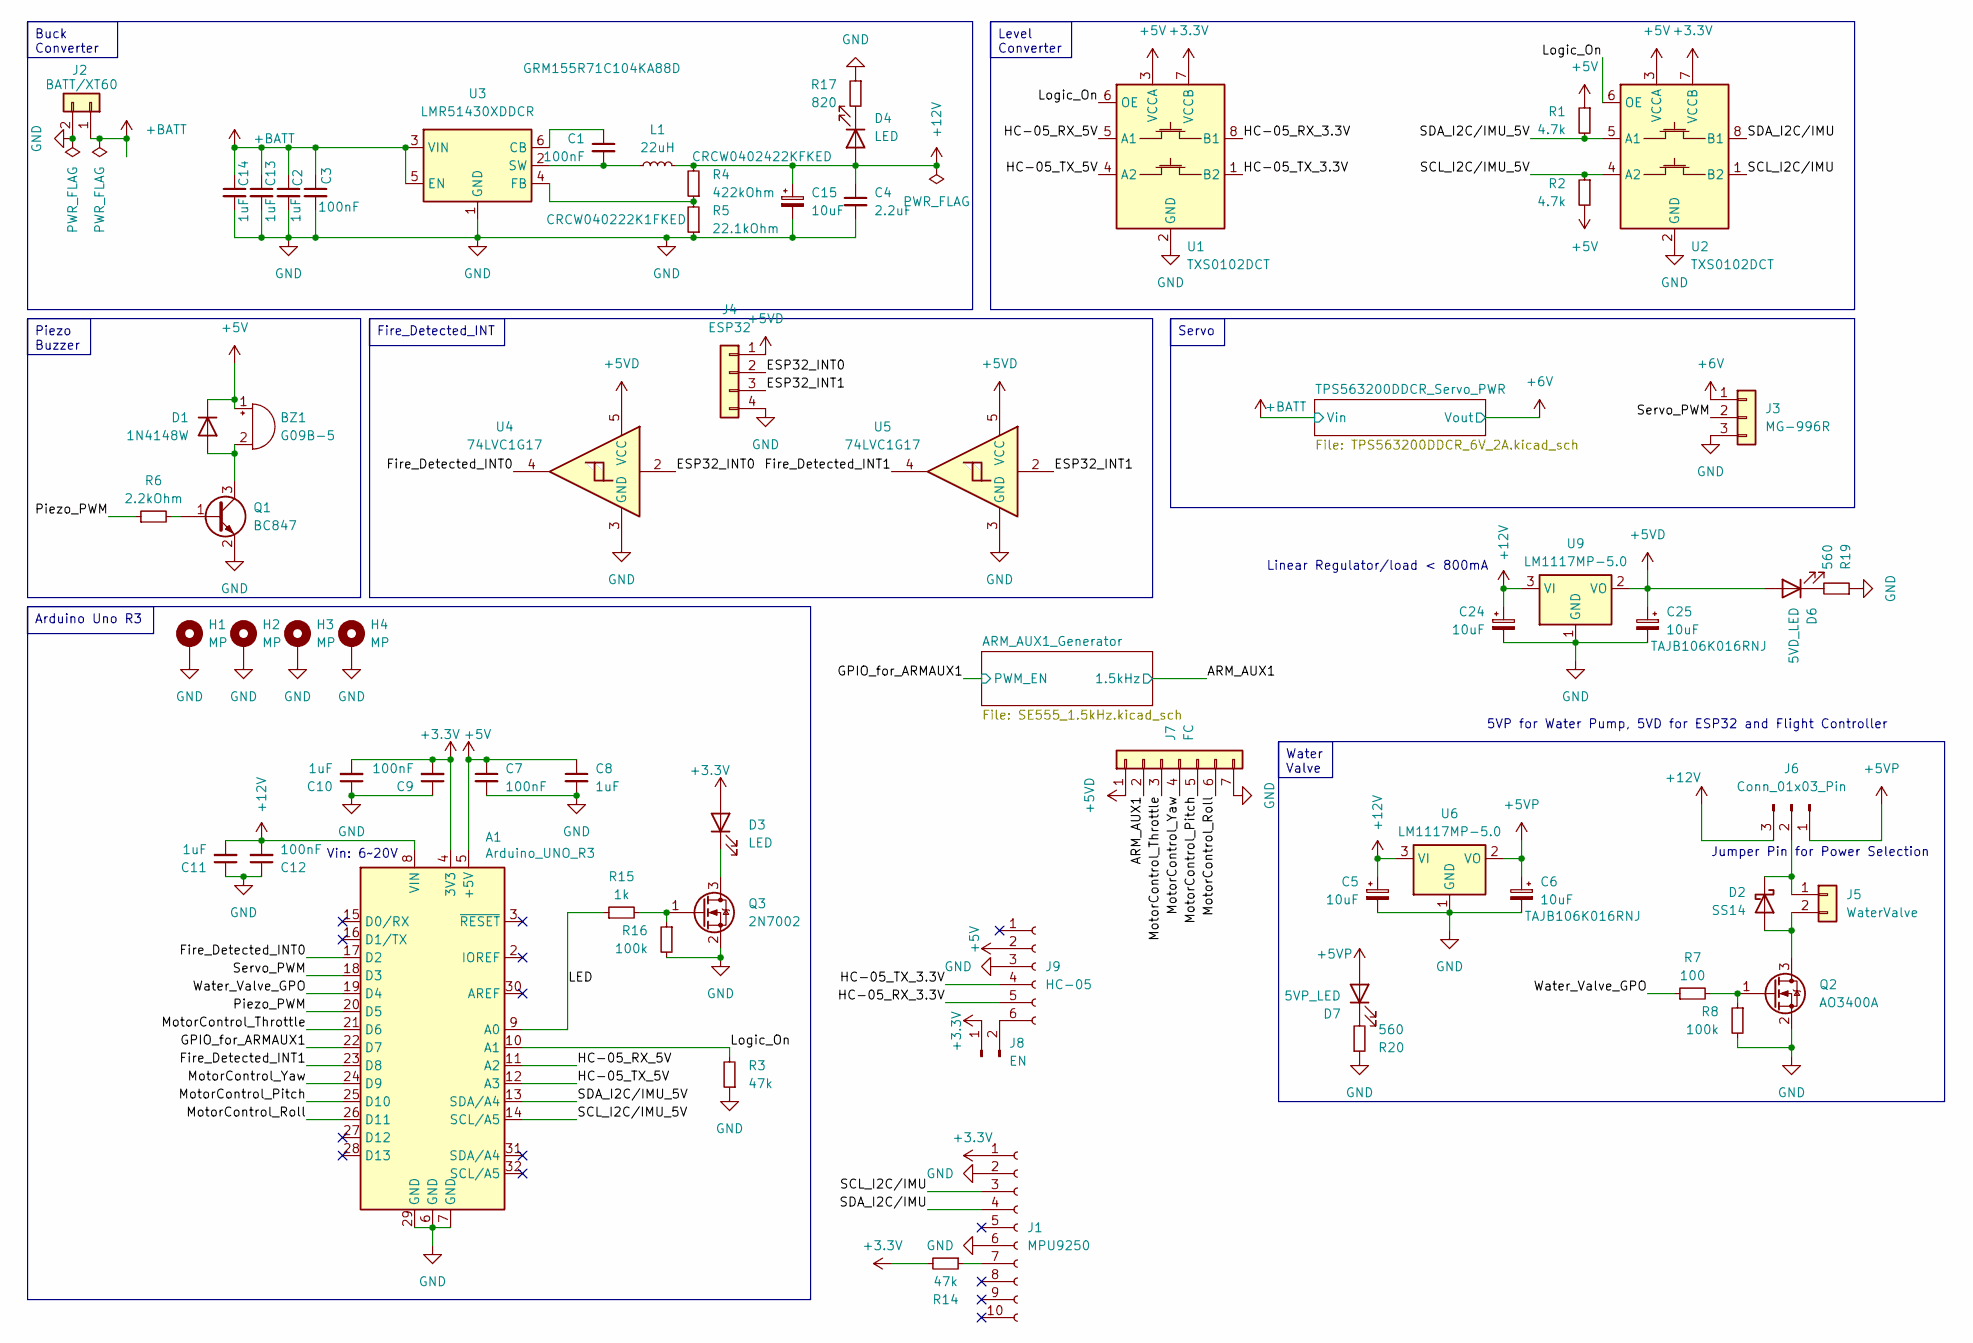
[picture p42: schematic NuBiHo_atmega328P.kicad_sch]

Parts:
A1: Arduino_UNO_R3
BZ1: G09B-5; [GEC] G09B-5
C1: 100nF; C_0402_1005Metric; Part No. GRM155R71C104KA88D
C2, C13, C14: 1uF; C_0603_1608Metric; Part No. GRM188R71E105KA12D
C3: 100nF; C_0805_2012Metric; Part No. GRM21BR71H104KA01L
C4: 2.2uF; C_0805_2012Metric; Part No. GRM21BR71C225KA12L
C5: 10uF; CP_EIA-3528-21_Kemet-B_Pad1.50x2.35mm_HandSolder
C6: 10uF; CP_EIA-3528-21_Kemet-B_Pad1.50x2.35mm_HandSolder; Part No. TAJB106K016RNJ
C7, C9, C12: 100nF; C_0402_1005Metric
C8, C10, C11: 1uF; C_0402_1005Metric
C15: 10uF; CP_EIA-6032-28_Kemet-C; Part No. 593D106X9025C2TE3
C24: 10uF; CP_EIA-3528-21_Kemet-B
C25: 10uF; CP_EIA-3528-21_Kemet-B; Part No. TAJB106K016RNJ
D1: 1N4148W; D_SOD-123
D2: SS14; D_SMA
D3, D4: LED; LED_0805_2012Metric
D6: 5VD_LED; LED_0805_2012Metric
D7: 5VP_LED; LED_0805_2012Metric
H1, H2, H3, H4: MP; MountingHole_3.2mm_M3_Pad_Via
J1: MPU9250; PinHeader_1x10_P2.54mm_Vertical
J2: BATT/XT60; AMASS_XT60-M_1x02_P7.20mm_Vertical
J3: MG-996R; Molex_SPOX_5267-03A_1x03_P2.50mm_Vertical
J4: ESP32; Molex_SPOX_5267-04A_1x04_P2.50mm_Vertical
J5: WaterValve; Molex_SPOX_5267-02A_1x02_P2.50mm_Vertical
J6: Conn_01x03_Pin; PinHeader_1x03_P2.54mm_Vertical
J7: FC; Molex_SPOX_5267-07A_1x07_P2.50mm_Vertical
J8: EN; PinHeader_1x02_P2.54mm_Vertical
J9: HC-05; PinHeader_1x06_P2.54mm_Vertical
L1: 22uH; INDPM172172X700N; Part No. IHLP6767GZER220M11
Q1: BC847; SOT-23
Q2: AO3400A; SOT-23
Q3: 2N7002; SOT-23
R1, R2: 4.7k; R_0402_1005Metric
R3, R14: 47k; R_0402_1005Metric
R4: 422kOhm; R_0603_1608Metric; Part No. CRCW0402422KFKED
R5: 22.1kOhm; R_0603_1608Metric; Part No. CRCW040222K1FKED
R6: 2.2kOhm; R_0402_1005Metric
R7: 100; R_0402_1005Metric
R8, R16: 100k; R_0402_1005Metric
R15: 1k; R_0402_1005Metric
R17: 820; R_0402_1005Metric
R19, R20: 560; R_0402_1005Metric
U1, U2: TXS0102DCT; SSOP-8_2.95x2.8mm_P0.65mm
U3: LMR51430XDDCR; SOT-23-6
U4, U5: 74LVC1G17; SOT-23-5
U6, U9: LM1117MP-5.0; SOT-223-3_TabPin2

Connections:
+3.3V: A1.4 (3V3), C9.2, C10.2, D3.2 (A), J1.1, J8.1, R14.2, U1.7 (VCCB), U2.7 (VCCB)
+5V: A1.5 (+5V), BZ1.1 (+), C7.1, C8.1, D1.1 (K), J9.2, R1.1, R2.2, U1.3 (VCCA), U2.3 (VCCA); also elsewhere on the board
+5VD: C25.1, D6.2 (A), J4.1, J7.1, U4.5 (VCC), U5.5 (VCC), U9.2 (VO)
+5VP: C6.1, D7.2 (A), J6.1, U6.2 (VO)
+6V: J3.1; also elsewhere on the board
+12V: A1.8 (VIN), C4.1, C5.1, C11.2, C12.2, C15.1, C24.1, D4.2 (A), J6.3, L1.2, R4.2, U6.3 (VI), U9.3 (VI)
+BATT: C2.1, C3.1, C13.1, C14.1, J2.1, U3.3 (VIN), U3.5 (EN); also elsewhere on the board
/ARM_AUX1: J7.2; also elsewhere on the board
/ESP32_INT0: J4.2, U4.2
/ESP32_INT1: J4.3, U5.2
/Fire_Detected_INT0: A1.17 (D2), U4.4
/Fire_Detected_INT1: A1.23 (D8), U5.4
/GPIO_for_ARMAUX1: A1.22 (D7); also elsewhere on the board
/HC-05_RX_3.3V: J9.5, U1.8 (B1)
/HC-05_RX_5V: A1.11 (A2), U1.5 (A1)
/HC-05_TX_3.3V: J9.4, U1.1 (B2)
/HC-05_TX_5V: A1.12 (A3), U1.4 (A2)
/LED: A1.9 (A0), R15.1
/Logic_On: A1.10 (A1), R3.2, U1.6 (OE), U2.6 (OE)
/MotorControl_Pitch: A1.25 (D10), J7.5
/MotorControl_Roll: A1.26 (D11), J7.6
/MotorControl_Throttle: A1.21 (D6), J7.3
/MotorControl_Yaw: A1.24 (D9), J7.4
/Piezo_PWM: A1.20 (D5), R6.1
/SCL_I2C/IMU: J1.3, U2.1 (B2)
/SCL_I2C/IMU_5V: A1.14 (SCL/A5), R2.1, U2.4 (A2)
/SDA_I2C/IMU: J1.4, U2.8 (B1)
/SDA_I2C/IMU_5V: A1.13 (SDA/A4), R1.2, U2.5 (A1)
/Servo_PWM: A1.18 (D3), J3.2
/Water_Valve_GPO: A1.19 (D4), R7.1
GND: A1.6 (GND), A1.7 (GND), A1.29 (GND), C2.2, C3.2, C4.2, C5.2, C6.2, C7.2, C8.2, C9.1, C10.1, C11.1, C12.1, C13.2, C14.2, C15.2, C24.2, C25.2, H1.1, H2.1, H3.1, H4.1, J1.2, J1.6, J2.2, J3.3, J4.4, J7.7, J9.3, Q1.2 (E), Q2.2 (S), Q3.2 (S), R3.1, R5.1, R8.2, R16.2, R17.1, R19.1, R20.1, U1.2 (GND), U2.2 (GND), U3.1 (GND), U4.3 (GND), U5.3 (GND), U6.1 (GND), U9.1 (GND); also elsewhere on the board
unnamed: BZ1.2 (-), D1.2 (A), Q1.3 (C)
unnamed: D2.2 (A), J5.2, Q2.3 (D)
unnamed: D2.1 (K), J5.1, J6.2
unnamed: D3.1 (K), Q3.3 (D)
unnamed: D4.1 (K), R17.2
unnamed: D6.1 (K), R19.2
unnamed: D7.1 (K), R20.2
unnamed: J1.7, R14.1
unnamed: J8.2, J9.6
unnamed: Q1.1 (B), R6.2
unnamed: Q2.1 (G), R7.2, R8.1
unnamed: Q3.1 (G), R15.2, R16.1
unnamed: C1.1, U3.6 (CB)
unnamed: R4.1, R5.2, U3.4 (FB)
unnamed: C1.2, L1.1, U3.2 (SW)

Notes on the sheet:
Vin: 6~20V
5VP for Water Pump, 5VD for ESP32 and Flight Controller
Linear Regulator/load < 800mA
Jumper Pin for Power Selection
Servo
Piezo Buzzer
Level Converter
Fire_Detected_INT
Arduino Uno R3
Water Valve
Buck Converter

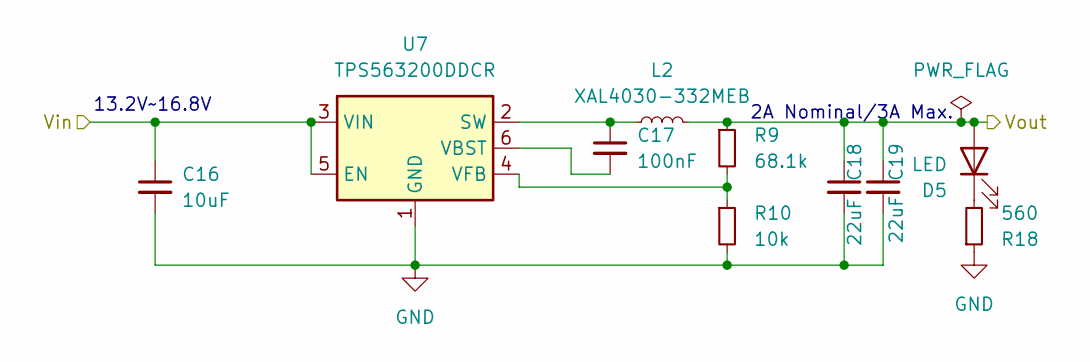
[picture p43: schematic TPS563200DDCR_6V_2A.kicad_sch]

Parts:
C16: 10uF; C_1206_3216Metric; Part No. GRM31CR61E106KA12L
C17: 100nF; C_0805_2012Metric; Part No. CC0805KRX7R9BB104
C18: 22uF; C_1206_3216Metric; Part No. GRM31CR71A226KE15L
C19: 22uF; C_1206_3216Metric
D5: LED; LED_0805_2012Metric
L2: XAL4030-332MEB; L_Coilcraft_XAL4030-XXX
R9: 68.1k; R_0603_1608Metric; Part No. RC0402FR-0768K1L
R10: 10k; R_0603_1608Metric; Part No. CRCW040210K0FKED
R18: 560; R_0402_1005Metric
U7: TPS563200DDCR; SOT-23-6

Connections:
+6V: C18.1, C19.1, D5.2 (A), L2.2, R9.1; also elsewhere on the board
+BATT: C16.1, U7.3 (VIN), U7.5 (EN); also elsewhere on the board
GND: C16.2, C18.2, C19.2, R10.2, R18.1, U7.1 (GND); also elsewhere on the board
unnamed: D5.1 (K), R18.2
unnamed: C17.1, L2.1, U7.2 (SW)
unnamed: C17.2, U7.6 (VBST)
unnamed: R9.2, R10.1, U7.4 (VFB)

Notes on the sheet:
2A Nominal/3A Max.
13.2V~16.8V

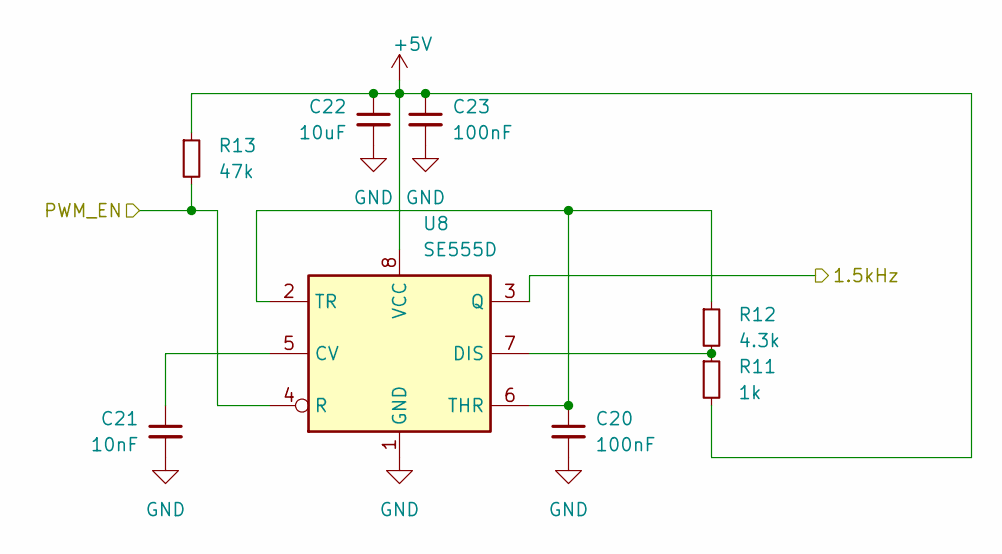
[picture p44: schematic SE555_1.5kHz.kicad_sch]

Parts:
C20: 100nF; C_1206_3216Metric
C21: 10nF; C_0603_1608Metric
C22: 10uF; C_0402_1005Metric
C23: 100nF; C_0402_1005Metric
R11: 1k; R_0402_1005Metric
R12: 4.3k; R_0402_1005Metric
R13: 47k; R_0402_1005Metric
U8: SE555D; SOIC-8_3.9x4.9mm_P1.27mm

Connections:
+5V: C22.1, C23.1, R11.2, R13.1, U8.8 (VCC); also elsewhere on the board
/ARM_AUX1: U8.3 (Q); also elsewhere on the board
/GPIO_for_ARMAUX1: R13.2, U8.4 (R); also elsewhere on the board
GND: C20.2, C21.2, C22.2, C23.2, U8.1 (GND); also elsewhere on the board
unnamed: C21.1, U8.5 (CV)
unnamed: R11.1, R12.2, U8.7 (DIS)
unnamed: C20.1, R12.1, U8.2 (TR), U8.6 (THR)

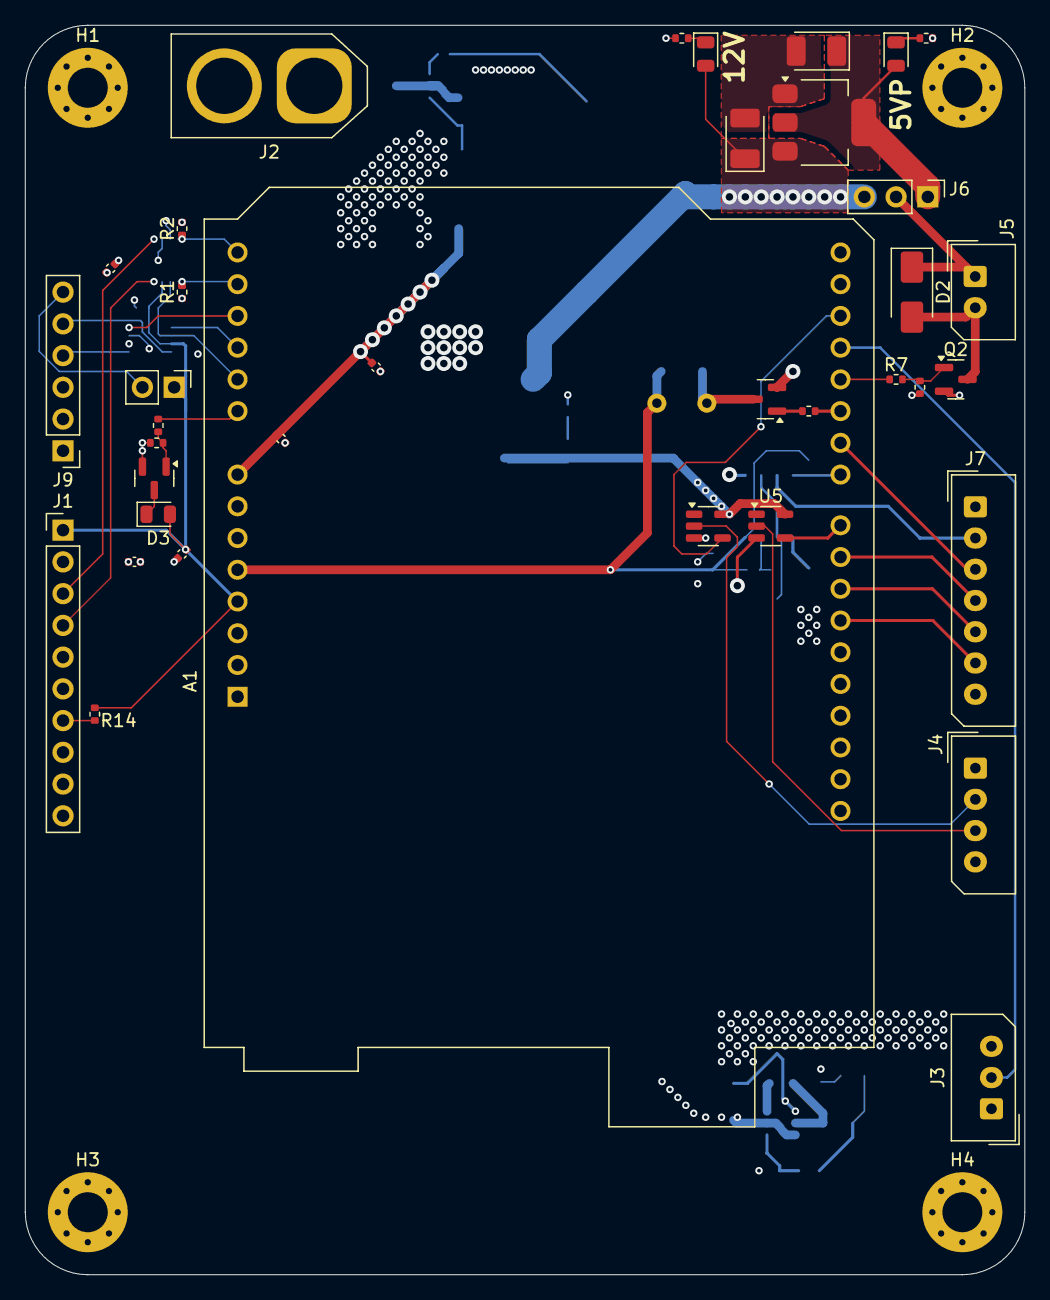
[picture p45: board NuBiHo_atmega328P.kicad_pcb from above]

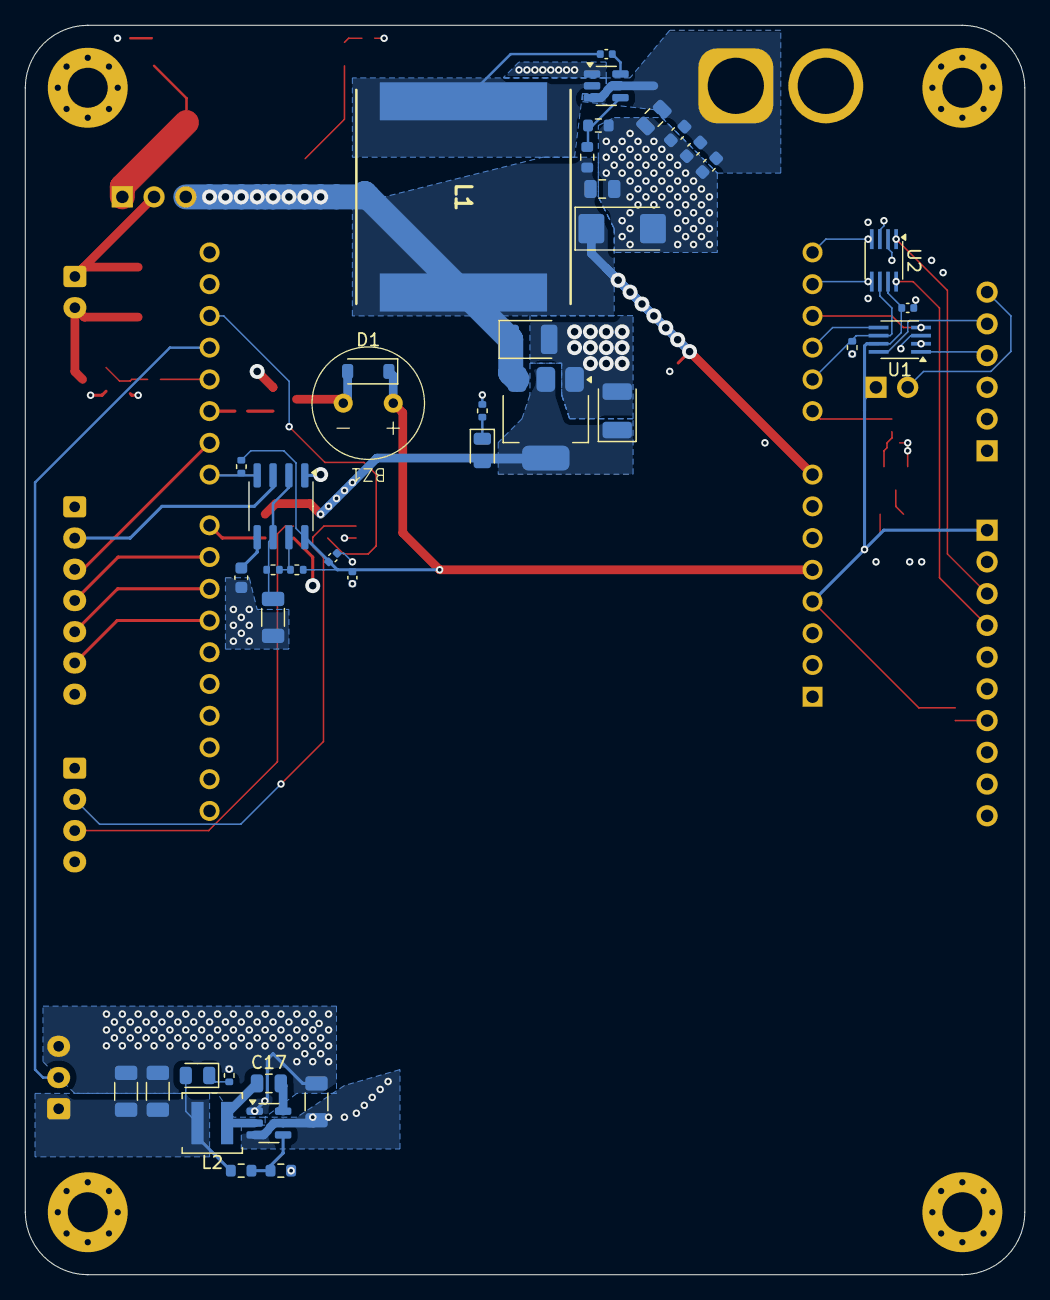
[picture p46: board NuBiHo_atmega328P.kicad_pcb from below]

Board: 4 copper layers, 80.0 x 100.0 mm, 81 parts (40 on the bottom side), 53 nets.

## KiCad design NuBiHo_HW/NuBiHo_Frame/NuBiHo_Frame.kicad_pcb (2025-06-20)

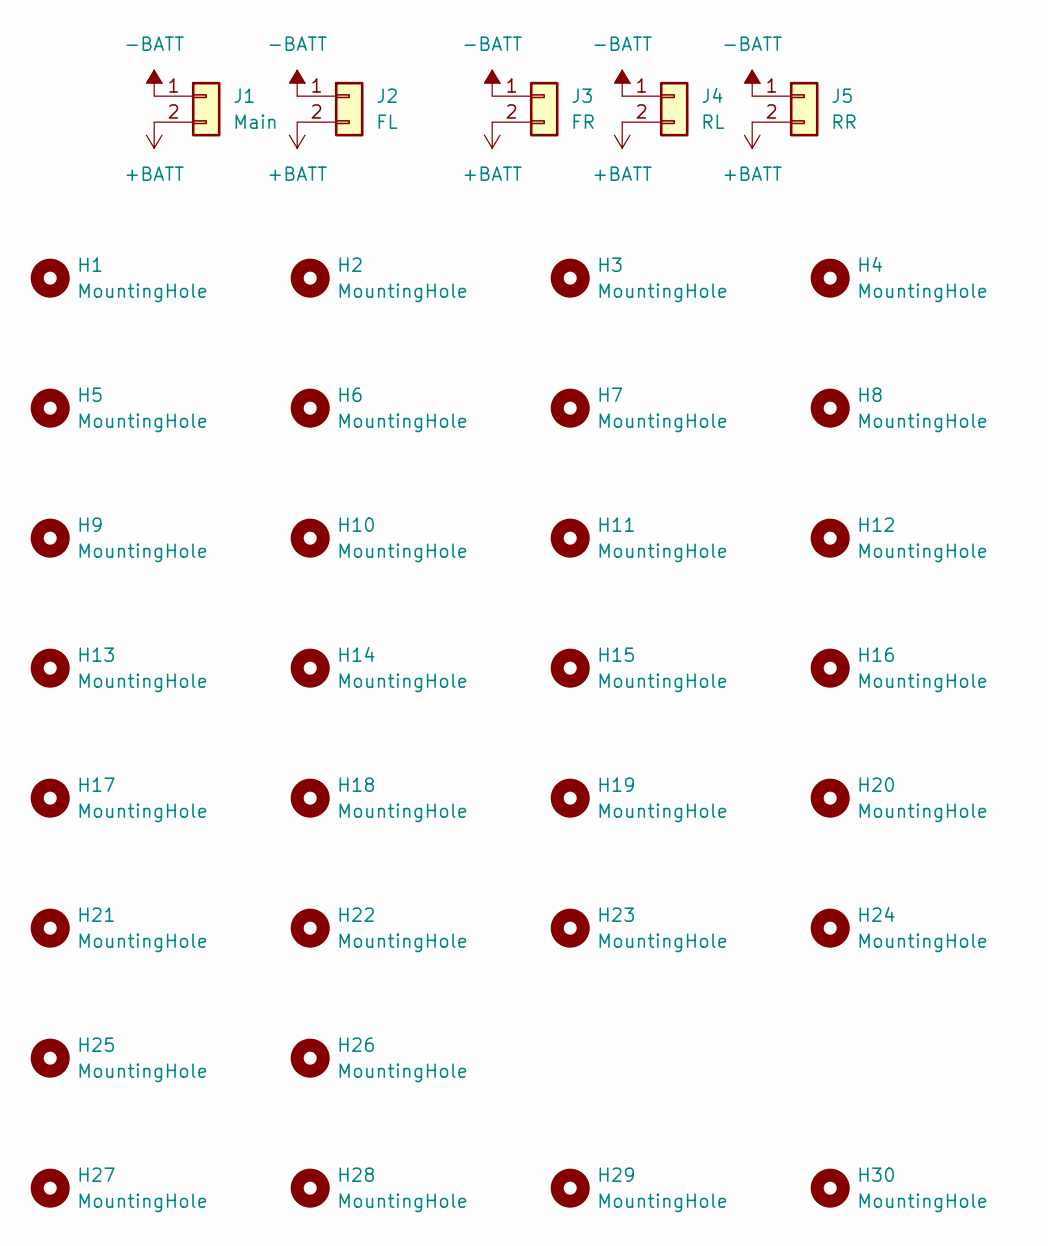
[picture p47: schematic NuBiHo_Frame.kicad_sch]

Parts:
H1, H2, H3, H4, H5, H6, H7, H8, H9, H10, H11, H12, H13, H14, H15, H16, H17, H18, H19, H20, H21, H22, H23, H24, H25, H26, H27, H28, H29, H30: MountingHole; MountingHole_3.2mm_M3_DIN965_Pad
J1: Main; AMASS_XT60-M_1x02_P7.20mm_Vertical
J2: FL; AMASS_XT60-M_1x02_P7.20mm_Vertical
J3: FR; AMASS_XT60-M_1x02_P7.20mm_Vertical
J4: RL; AMASS_XT60-M_1x02_P7.20mm_Vertical
J5: RR; AMASS_XT60-M_1x02_P7.20mm_Vertical

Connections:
+BATT: J1.2, J2.2, J3.2, J4.2, J5.2
-BATT: J1.1, J2.1, J3.1, J4.1, J5.1

Board: 2 copper layers, 35 parts (0 on the bottom side), 2 nets, no tracks yet.

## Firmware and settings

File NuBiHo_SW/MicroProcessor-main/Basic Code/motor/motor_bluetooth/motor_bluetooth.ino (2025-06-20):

#include <SoftwareSerial.h>
#include <Arduino.h>

// PWM 핀 정의
#define ROLL_PIN     11
#define PITCH_PIN    10
#define THROTTLE_PIN 6
#define YAW_PIN      9
#define AUX_PIN     3  // ARM 신호용

SoftwareSerial mySerial(A2, A3); // HC-05 연결 (RX=12, TX=13)

int rollPWM     = 1500;
int pitchPWM    = 1500;
int throttlePWM = 885;
int yawPWM      = 1000;
int auxPWM      = 1000;

int pwmStep     = 10;
bool armState   = false;
bool lastBtnEState = false;

unsigned long lastPWMTime = 0;
const int pwmPeriod = 20000; // 20ms 주기 (μs)

void setup() {
  pinMode(ROLL_PIN, OUTPUT);
  pinMode(PITCH_PIN, OUTPUT);
  pinMode(THROTTLE_PIN, OUTPUT);
  pinMode(YAW_PIN, OUTPUT);
  pinMode(AUX_PIN, OUTPUT);
  pinMode(A1, OUTPUT);
  digitalWrite(A1, HIGH);

  Serial.begin(9600);
  mySerial.begin(38400);
}

void loop() {
  if (mySerial.available()) {
    String line = mySerial.readStringUntil('\n');
    line.trim();

    int arrowPos = line.indexOf(">>");
    if (arrowPos != -1) {
      line = line.substring(arrowPos + 2);
      line.trim();
    }

    int c1 = line.indexOf(',');
    int c2 = line.indexOf(',', c1 + 1);

    if (c1 > 0 && c2 > c1) {
      int rawX = line.substring(0, c1).toInt();
      int rawY = line.substring(c1 + 1, c2).toInt();
      String btn = line.substring(c2 + 1);
      btn.trim();

      // 버튼 A/B → Pitch 조절
      if (btn.indexOf('A') != -1) pitchPWM += pwmStep;
      if (btn.indexOf('B') != -1) pitchPWM -= pwmStep;

      // 버튼 C/D → Throttle 조절
      if (btn.indexOf('C') != -1) throttlePWM += pwmStep;
      if (btn.indexOf('D') != -1) throttlePWM -= pwmStep;

      // ✅ 버튼 E → 토글 방식 ARM 제어
      bool currentBtnE = btn.indexOf('E') != -1;
      if (currentBtnE && !lastBtnEState) {
        armState = !armState;  // 상태 반전
        Serial.print("[ARM TOGGLE] -> ");
        Serial.println(armState ? "ON" : "OFF");
      }
      lastBtnEState = currentBtnE;

      // 조이스틱 → Roll/Yaw
      if (rawX < 333) rollPWM = map(rawX, 0, 333, 1000, 1500);
      else            rollPWM = map(rawX, 333, 675, 1500, 2000);

      if (rawY < 333) yawPWM = map(rawY, 0, 333, 1000, 1500);
      else            yawPWM = map(rawY, 333, 675, 1500, 2000);

      rollPWM     = constrain(rollPWM,     1000, 2000);
      pitchPWM    = constrain(pitchPWM,    1000, 2000);
      throttlePWM = constrain(throttlePWM, 1000, 2000);
      yawPWM      = constrain(yawPWM,      1000, 2000);

      auxPWM = armState ? 1600 : 1000;

      Serial.print("ROLL: "); Serial.print(rollPWM);
      Serial.print("  PITCH: "); Serial.print(pitchPWM);
      Serial.print("  THR: "); Serial.print(throttlePWM);
      Serial.print("  YAW: "); Serial.print(yawPWM);
      Serial.print("  AUX: "); Serial.println(auxPWM);
    }
  }

  // 20ms 주기로 PWM 출력
  if (micros() - lastPWMTime >= pwmPeriod) {
    lastPWMTime = micros();
    sendPWM(rollPWM, pitchPWM, throttlePWM, yawPWM, auxPWM);
  }
}

void sendPWM(int roll, int pitch, int throttle, int yaw, int aux) {
  digitalWrite(ROLL_PIN, HIGH);
  digitalWrite(PITCH_PIN, HIGH);
  digitalWrite(THROTTLE_PIN, HIGH);
  digitalWrite(YAW_PIN, HIGH);
  digitalWrite(AUX_PIN, HIGH);

  unsigned long start = micros();
  bool roll_done = false, pitch_done = false;
  bool throttle_done = false, yaw_done = false, aux_done = false;

  while (micros() - start < 2200) {
    unsigned long elapsed = micros() - start;

    if (!roll_done && elapsed >= roll)         { digitalWrite(ROLL_PIN, LOW); roll_done = true; }
    if (!pitch_done && elapsed >= pitch)       { digitalWrite(PITCH_PIN, LOW); pitch_done = true; }
    if (!throttle_done && elapsed >= throttle) { digitalWrite(THROTTLE_PIN, LOW); throttle_done = true; }
    if (!yaw_done && elapsed >= yaw)           { digitalWrite(YAW_PIN, LOW); yaw_done = true; }
    if (!aux_done && elapsed >= aux)           { digitalWrite(AUX_PIN, LOW); aux_done = true; }
  }

  if (!roll_done)     digitalWrite(ROLL_PIN, LOW);
  if (!pitch_done)    digitalWrite(PITCH_PIN, LOW);
  if (!throttle_done) digitalWrite(THROTTLE_PIN, LOW);
  if (!yaw_done)      digitalWrite(YAW_PIN, LOW);
  if (!aux_done)      digitalWrite(AUX_PIN, LOW);
}

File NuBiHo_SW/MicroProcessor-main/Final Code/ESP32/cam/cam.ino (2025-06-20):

/********************************************************************
 * ESP32-CAM : Red Area Detection
 *   – 빨강 비율이 0.27 이상인 프레임이 5 연속 → 두 핀 HIGH
 *   – 빨강 비율이 0.23 이하인 프레임이 5 연속 → 두 핀 LOW
 *   – ON 상태 : GPIO12, GPIO4 모두 HIGH (100 %)
 ********************************************************************/
#include <Arduino.h>
#include "esp_camera.h"

#define CAMERA_MODEL_AI_THINKER
#include "camera_pins.h"

/* ---------- 사용자 설정 ---------- */
#define PIN_LED1      12          // LED 1 (100 %)
#define PIN_LED2      4           // LED 2 (100 %)
#define FRAME_SIZE    FRAMESIZE_QQVGA   // 160×120
#define TH_ON_RATIO   0.23        // 켤 때 기준
#define TH_OFF_RATIO  0.18        // 끌 때 기준
#define TH_FRAMES     5           // 연속 프레임 수
/* ---------------------------------- */

/* 빨강 판별 함수 (RGB565 → 8-bit RGB) */
inline bool isRed(uint16_t rgb565)
{
  uint8_t r = ((rgb565 >> 11) & 0x1F) * 255 / 31;
  uint8_t g = ((rgb565 >>  5) & 0x3F) * 255 / 63;
  uint8_t b = ( rgb565        & 0x1F) * 255 / 31;
  return (r > 120) && (r > g + 30) && (r > b + 30);
}

void setup()
{
  Serial.begin(115200);

  /* 출력 핀 초기화 */
  pinMode(PIN_LED1, OUTPUT);
  pinMode(PIN_LED2, OUTPUT);
  digitalWrite(PIN_LED1, LOW);
  digitalWrite(PIN_LED2, LOW);

  /* 카메라 설정 */
  camera_config_t cfg;
  cfg.ledc_channel = LEDC_CHANNEL_0;
  cfg.ledc_timer   = LEDC_TIMER_0;
  cfg.pin_d0 = Y2_GPIO_NUM;  cfg.pin_d1 = Y3_GPIO_NUM;  cfg.pin_d2 = Y4_GPIO_NUM;
  cfg.pin_d3 = Y5_GPIO_NUM;  cfg.pin_d4 = Y6_GPIO_NUM;  cfg.pin_d5 = Y7_GPIO_NUM;
  cfg.pin_d6 = Y8_GPIO_NUM;  cfg.pin_d7 = Y9_GPIO_NUM;
  cfg.pin_xclk = XCLK_GPIO_NUM;  cfg.pin_pclk = PCLK_GPIO_NUM;
  cfg.pin_vsync = VSYNC_GPIO_NUM; cfg.pin_href = HREF_GPIO_NUM;
  cfg.pin_sccb_sda = SIOD_GPIO_NUM; cfg.pin_sccb_scl = SIOC_GPIO_NUM;
  cfg.pin_pwdn = PWDN_GPIO_NUM; cfg.pin_reset = RESET_GPIO_NUM;
  cfg.xclk_freq_hz = 20000000;
  cfg.pixel_format = PIXFORMAT_RGB565;   // RAW
  cfg.frame_size   = FRAME_SIZE;
  cfg.jpeg_quality = 12;
  cfg.fb_count     = 1;

  if (esp_camera_init(&cfg) != ESP_OK) {
    Serial.println("Camera init failed");
    while (true) delay(1000);
  }
  Serial.println("Start red-area detection");
}

void loop()
{
  camera_fb_t *fb = esp_camera_fb_get();
  if (!fb) return;

  /* 빨강 픽셀 계산 */
  uint16_t *pix = (uint16_t *)fb->buf;
  size_t tot = fb->len >> 1, red = 0;
  for (size_t i = 0; i < tot; ++i)
    if (isRed(pix[i])) ++red;
  esp_camera_fb_return(fb);

  float ratio = (float)red / tot;

  /* 히스테리시스 + 디바운스 */
  static uint8_t onCnt = 0, offCnt = 0;
  static bool    state = false;          // 현재 LED 상태

  if (!state) {                          // 현재 OFF
    if (ratio >= TH_ON_RATIO) {
      if (++onCnt >= TH_FRAMES) {        // 조건 충족 → ON
        state = true;  onCnt = 0;
        digitalWrite(PIN_LED1, HIGH);
        digitalWrite(PIN_LED2, HIGH);
      }
    } else onCnt = 0;
  } else {                               // 현재 ON
    if (ratio < TH_OFF_RATIO) {
      if (++offCnt >= TH_FRAMES) {       // 조건 충족 → OFF
        state = false; offCnt = 0;
        digitalWrite(PIN_LED1, LOW);
        digitalWrite(PIN_LED2, LOW);
      }
    } else offCnt = 0;
  }

  /* 30 프레임마다 디버그 출력 */
  static uint32_t f = 0;
  if (++f % 30 == 0)
    Serial.printf("#%lu  red=%u  tot=%u  r=%.3f  LED=%s\n",
                  f, red, tot, ratio, state ? "ON" : "OFF");

  delay(30);                              // ≈25–30 fps
}

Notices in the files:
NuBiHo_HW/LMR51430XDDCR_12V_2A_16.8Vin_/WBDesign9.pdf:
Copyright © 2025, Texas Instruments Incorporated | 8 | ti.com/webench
